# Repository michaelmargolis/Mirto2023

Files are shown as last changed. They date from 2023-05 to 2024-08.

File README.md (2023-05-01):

# Mirto2023
This repository contains software and CAD files for the 2023 version of
the Middlesex University robot platform used for CS and outreach.

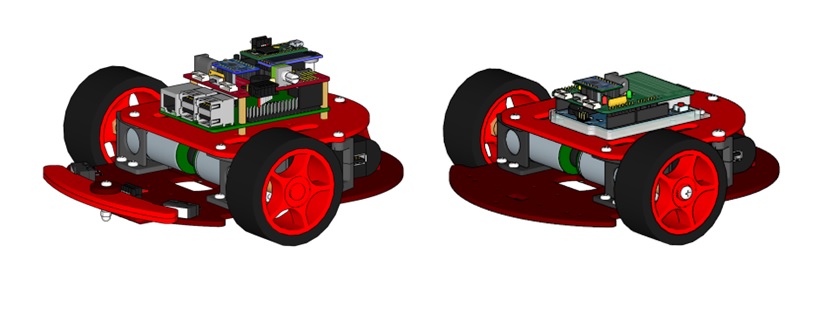
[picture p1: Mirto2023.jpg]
Mirto 2023


Build documentation

This version supports the following variants:
* CS Mirto using Teensy 3.2 board and Raspberry Pi 
  * Teensy drives robot hardware
  * Pi supports robot logic in high level language (python, racket etc)
  * Communication between teensy and Pi using ASIP protocol (see ASIP 1.2 repo)
  * two legacy PCBs are supported:
    * Mirto2016 board that uses Toshiba TB6612FNG H-Bridge
    * Mirto2018 board using TI DRV8833 H-Bridge
  
* CS Mirto using Pico 2040 and Raspbery Pi
  * similar to above but using Pico instead of Teensy
  
* Outreach Mirto using Pico WiFI
  * Uses same Pico PCB as CS pico but without Raspberry pi
  * ASIP protocol over WiFI connects to Scratch or similar
  
* Outreach Mirto using Arduino Wifi R2
  * Uses custom shield for H-Bridge and other robot hardware support
  * ASIP protocol over WiFI connects to Scratch or similar
  
* Standalone Mirto
  * This comprises any of the above without the Raspberry PI
  * Robot logic onboard in C++ or micropython depending on microcontroller

See the ASIP 1.2 repository for code needed for the CS version 

A research paper providing context for use of this robot at Middlesex University can be found here https://eprints.mdx.ac.uk/24368/

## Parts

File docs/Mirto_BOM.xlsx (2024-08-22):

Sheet: Mirto2023
Pico Robot |  | Nbr of Robots | 15
Description | order link | Quantity (per robot) | Total quantity | On hand
PCB Components (Farnell unless indicated)
1K resistor | 9343253 | 2 | 30 |  | all resistors are 1/8th watt
330R resistor | 9343032 | 2
100uF cap | 1870997 | 1 | 15
0.1uF cap | 1141775 | 3 | 45
2.2uF cap | 1827838 | 1 | 15
4.7k resistor network | 9356100 | 2 | 30
PMEG3050EP 5A schottky | 1829197 | 2 | 30
Motor switch | 1201431 | 1 | 15
1N4148 | 9843680 | 1 | 15
BAT46 | 9801456 | 1 | 15
3mm red led | 1581112 | 1 | 15
3mm green led | 1581114 | 1 | 15
8 pin female header | 1593463 | 1 | 15
6 pin female header | 1593462 | 1 | 15
20 pin female header | 1593469 | 2 | 30
2x3 female IDC receptacle | 2215230 | 1 | 15
2x2 female IDC receptacle | 2886085 | 1 | 15
motor connectors | 9491848 | 2 | 30 |  | JST ZH
DC Jack | 224959 | 1 | 15
drv8833 adafruit h-bridge | 1528-1795-ND | 1 | 15 |  | digikey (or https://www.aliexpress.com/item/CJMCU-8833-DRV8833-stepper-motor-drive-control-dual-channel-H-bridge-motor-drive-module-winder/32862868838.html
5mm or 8mm neopixel | ADA1938 | 1 | 15 |  | pihut SKU: ADA1938
1.14 inch 240x135 LCD | WAV-18231 | 1 | 15 |  | Waveshare - pihut etc
20cm USBA to DC 2.1 barrel |  | 1 | 15 |  | https://www.aliexpress.com/item/USB-to-5-5-2-1mm-DC-Power-Barrel-Jack-Plug-5-5-x-2-1/32879860036.html
Male break-away headers |  |  |  |  | We should have in labs
Hardware
M3 12mm | 1420391 | 4 | 60 |  | Packs of 100, adjust order quantity accordingly
M3 8mm | 1419987 | 12 | 180 |  | Packs of 100, adjust order quantity accordingly
M3 5mm button head |  | 4 | 60 |  | Packs of 100, adjust order quantity accordingly
M3 nut | 1419447 | 16 | 240 |  | Packs of 100, adjust order quantity accordingly
M4 8mm | 1419992 | 6 | 90 |  | Packs of 100, adjust order quantity accordingly
1/10 scale wheels | AliExpress | 2 | 30 |  | https://www.aliexpress.com/item/4Pcs-lot-Rubber-63mm-Wheel-Flat-run-Tires-Wide-26mm-On-Road-For-1-10-RC/32759346320.html
Caster |  | 1 | 15 |  | https://www.bearingboys.co.uk/Light-Duty--Saturn-Type/LD16-Chrome-Ball-Transfer-Unit-48126-p
USB power pack |  | 1 | 15 |  | https://www.amazon.co.uk/dp/B019GJLER8
3D and acrylic parts |  |  |  |  | https://livemdxac-my.sharepoint.com/:f:/r/personal/m_margolis_mdx_ac_uk/Documents/Mirto%20Design%20Files/Arduino%20Robot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
motor bracket |  | 2 | 30
wheel hub |  | 2 | 30
acrylic parts
Alternative options for power cable
DC barrel cable | CP-2189-ND |  |  | digikey
USB A plug | 1175-1009-ND |  |  | digikey

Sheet: Arduino Mirto
Arduino Robot |  | Nbr of Robots | 12
Description | order link | Quantity (per robot) | Total quantity | On hand
PCB Components (Farnell unless indicated)
1K resistor | 9339051 | 3 | 36 | * | * Std 1/4 watt, we can use parts in labs
680 ohm | 9339655 | 1 | 12 | * | * Std 1/4 watt, we can use parts in labs
4.7k resistor network | 9356100 | 1 | 12
STPS2L60 2A schottky | 9907637 | 1 | 12
Motor switch | 1201431 | 1 | 12
3mm red led | 1581112 | 1 | 12
3mm green led | 1581114 | 1 | 12
3mm orange led | 1581141 | 1 | 12
8 pin female header | 1593463 | 1 | 12
6 pin female header | 1593462 | 1 | 12
motor connectors | 9491848 | 2 | 24 |  | JST ZH
DC Jack | 224959 | 1 | 12
drv8833 adafruit h-bridge | 1528-1795-ND | 1 | 12 |  | digikey (or https://www.aliexpress.com/item/CJMCU-8833-DRV8833-stepper-motor-drive-control-dual-channel-H-bridge-motor-drive-module-winder/32862868838.html
20cm USBA to DC 2.1 barrel |  | 1 | 12 |  | https://www.aliexpress.com/item/USB-to-5-5-2-1mm-DC-Power-Barrel-Jack-Plug-5-5-x-2-1/32879860036.html
Male break-away headers |  |  |  |  | We should have in labs
Hardware
M3 12mm | 1420391 | 4 | 48 |  | Packs of 100, adjust order quantity accordingly
M3 8mm | 1419987 | 12 | 144 |  | Packs of 100, adjust order quantity accordingly
M3 5mm button head |  | 4 | 48 |  | Packs of 100, adjust order quantity accordingly
M3 nut | 1419447 | 16 | 192 |  | Packs of 100, adjust order quantity accordingly
M4 8mm | 1419992 | 6 | 72 |  | Packs of 100, adjust order quantity accordingly
1/10 scale wheels | AliExpress | 2 | 24 |  | https://www.aliexpress.com/item/4Pcs-lot-Rubber-63mm-Wheel-Flat-run-Tires-Wide-26mm-On-Road-For-1-10-RC/32759346320.html
Caster |  | 1 | 12 |  | https://www.bearingboys.co.uk/Light-Duty--Saturn-Type/LD16-Chrome-Ball-Transfer-Unit-48126-p
USB power pack |  | 1 | 12 |  | https://www.amazon.co.uk/dp/B019GJLER8
3D and acrylic parts |  |  |  |  | https://livemdxac-my.sharepoint.com/:f:/r/personal/m_margolis_mdx_ac_uk/Documents/Mirto%20Design%20Files/Arduino%20Robot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
motor bracket |  | 2 | 24
wheel hub |  | 2 | 24
acrylic parts
Alternative options for power cable
DC barrel cable | CP-2189-ND |  |  | digikey
USB A plug | 1175-1009-ND |  |  | digikey

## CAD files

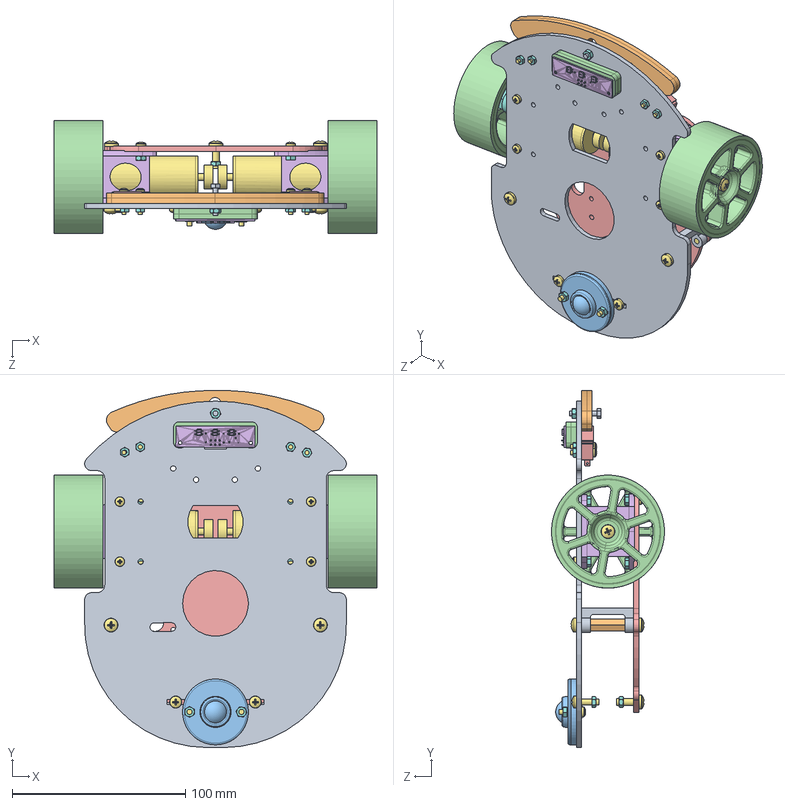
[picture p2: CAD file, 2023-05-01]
CAD/3D/Assembly/mirto2023.SLDASM
186.5 x 206.3 x 65.3 mm
top_plate
ir_spacer x 2
caster_spacer
bumper x 2
bottom_plate
Hotec Motor Mountv2 x 2
hotec_motor x 2
Motor hub x 2
offset_standoff
m4 standoffx30
ball wheel
1_10-drift-tire x 2
microswitch x 2
ir board
pan cross head_am x 23
hex nut style 1_am x 17
hex screw_am

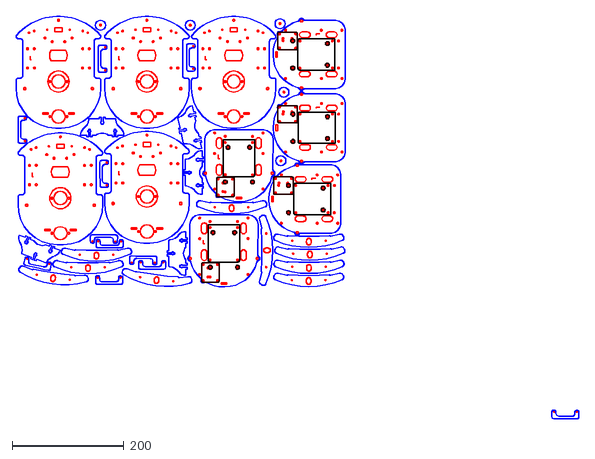
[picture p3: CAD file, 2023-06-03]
CAD/2D/arduino robot half sheet r12.dxf
1007.9 x 720.2

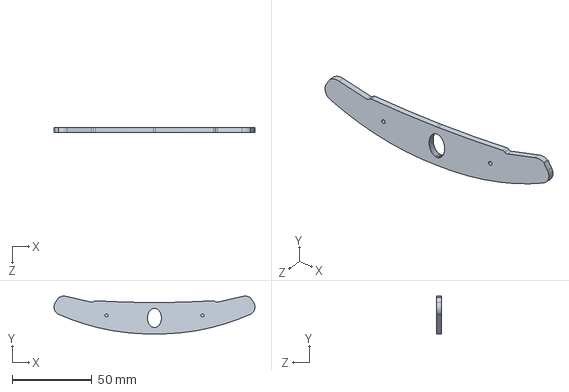
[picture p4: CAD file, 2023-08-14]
CAD/3D/Assembly/bumper.SLDPRT
125.7 x 23.7 x 3.00 mm

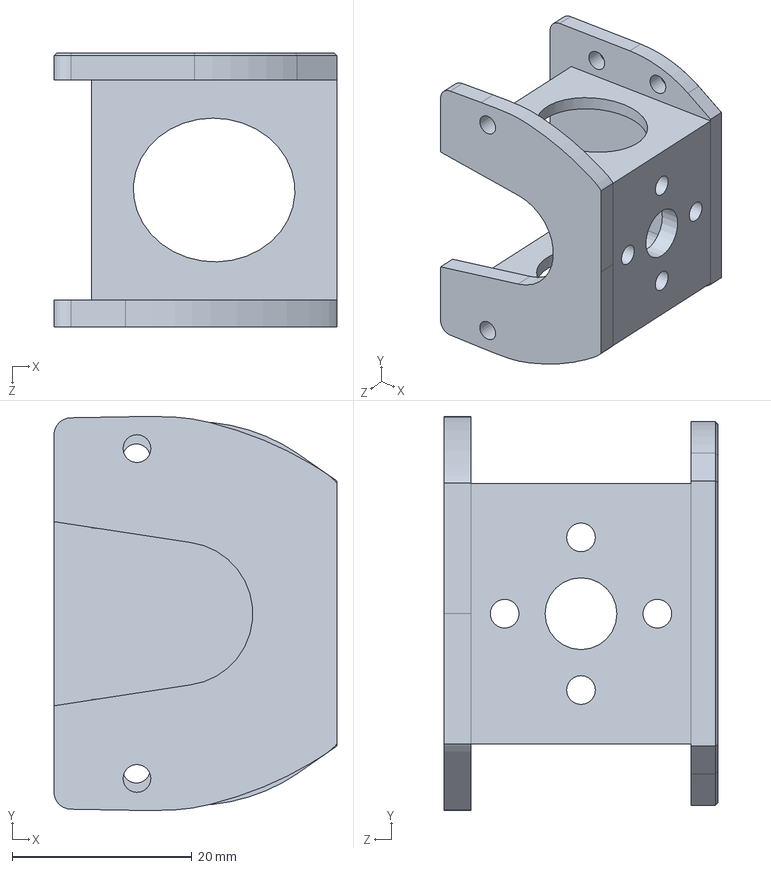
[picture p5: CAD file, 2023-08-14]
CAD/3D/Solidworks/Hotec Motor Mountv2.SLDPRT
31.5 x 43.9 x 30.5 mm

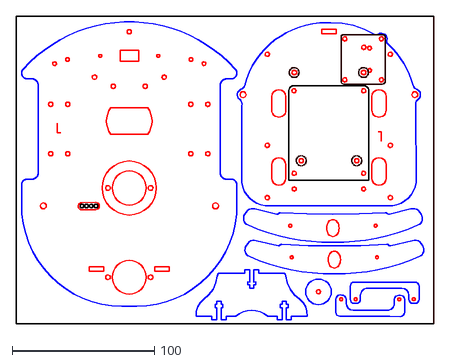
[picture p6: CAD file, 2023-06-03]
CAD/2D/one mirto2023.dxf
293.4 x 216.3

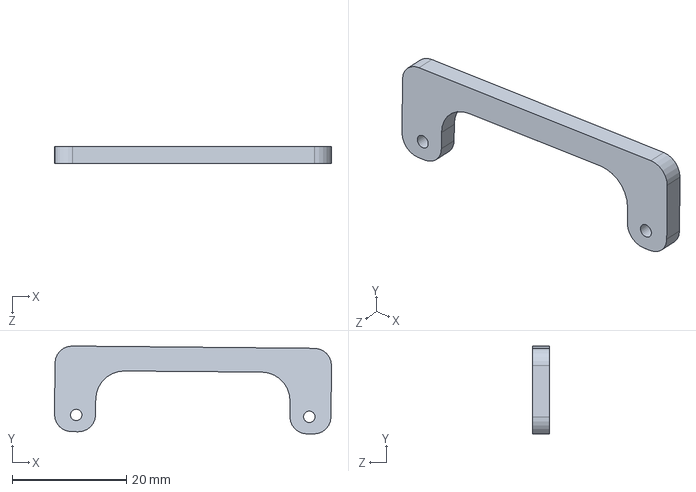
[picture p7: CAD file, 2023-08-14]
CAD/3D/Assembly/ir_spacer.SLDPRT
48.5 x 15.4 x 3.00 mm

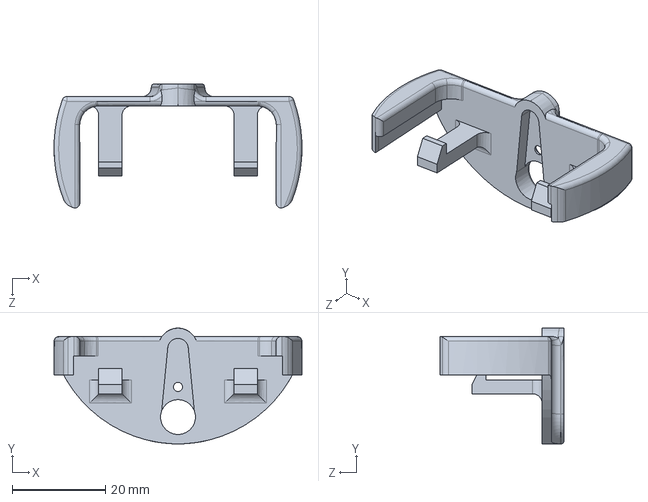
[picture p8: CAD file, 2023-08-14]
CAD/3D/Solidworks/hc_sro4_holder_v2.SLDPRT
53.1 x 24.8 x 26.6 mm

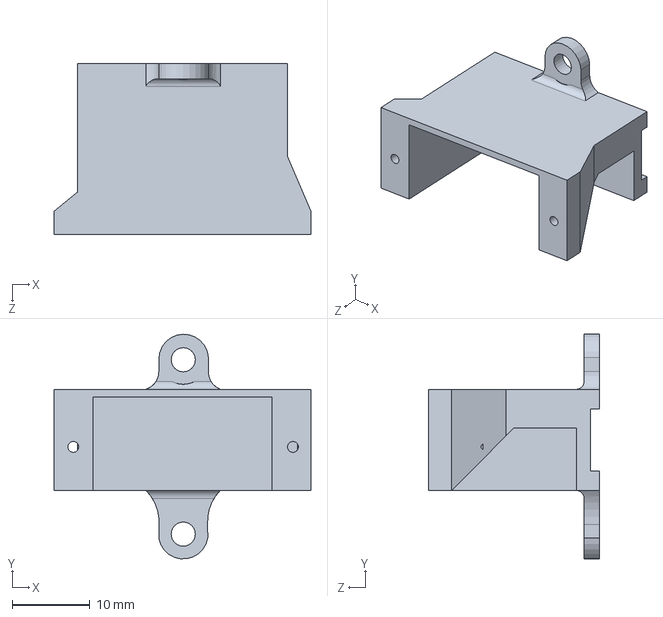
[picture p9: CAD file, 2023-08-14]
CAD/3D/Solidworks/9g servo mount.SLDPRT
33.0 x 28.8 x 22.0 mm

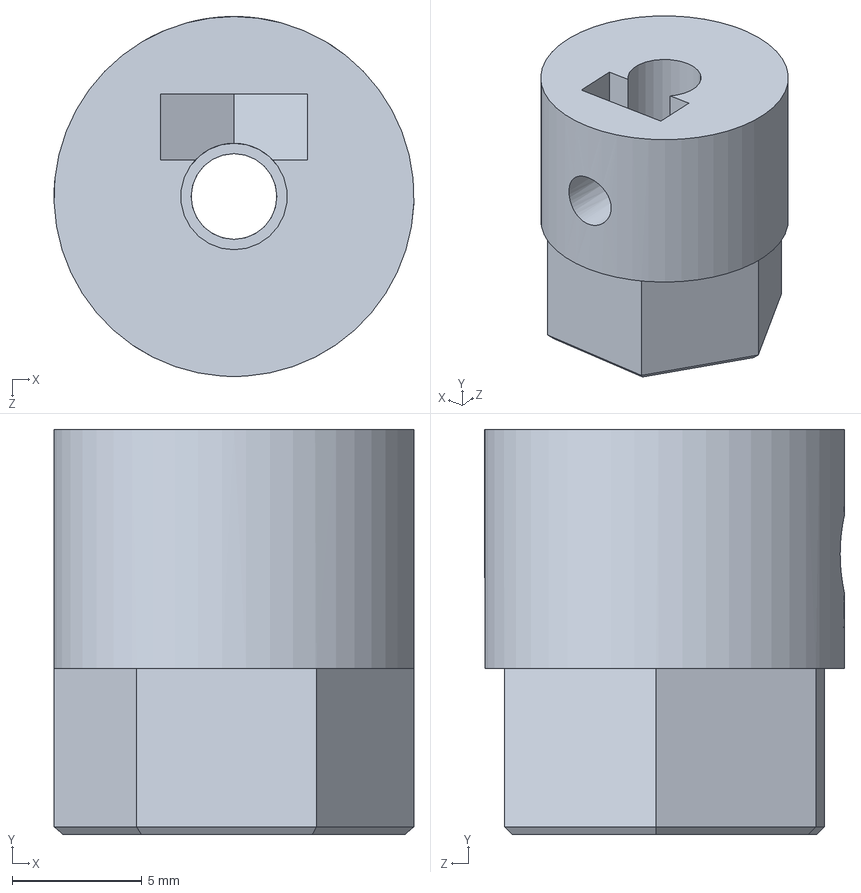
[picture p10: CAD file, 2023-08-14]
CAD/3D/Solidworks/Motor hub.SLDPRT
13.8 x 15.6 x 13.9 mm

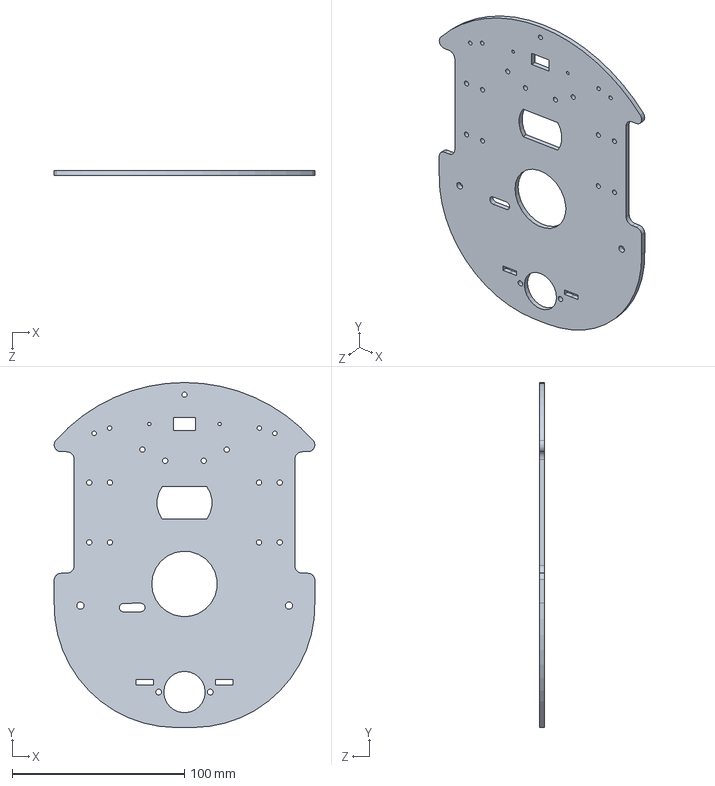
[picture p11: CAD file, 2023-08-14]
CAD/3D/Assembly/bottom_plate.SLDPRT
151.3 x 200.2 x 3.00 mm

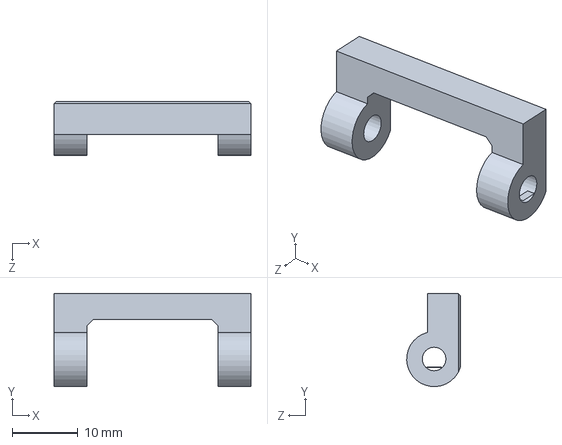
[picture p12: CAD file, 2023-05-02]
CAD/3D/Solidworks/offset_standoff.SLDPRT
30.0 x 14.2 x 8.17 mm

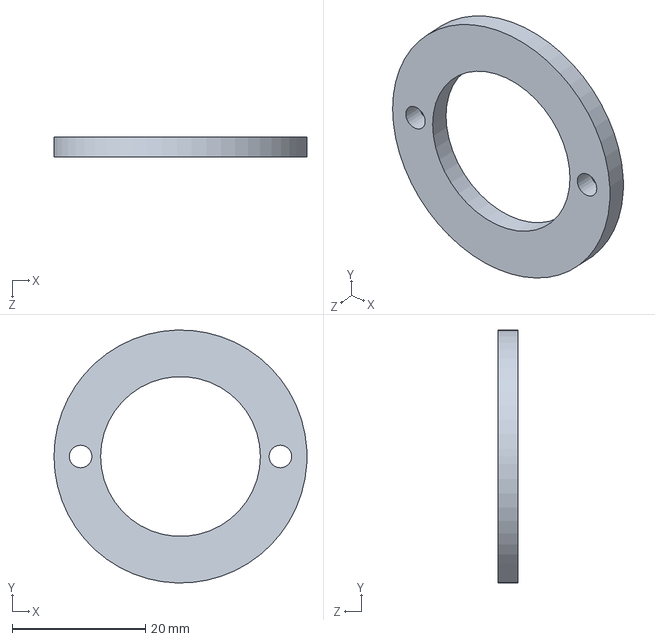
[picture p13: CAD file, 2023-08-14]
CAD/3D/Assembly/caster_spacer.SLDPRT
38.0 x 38.0 x 3.00 mm

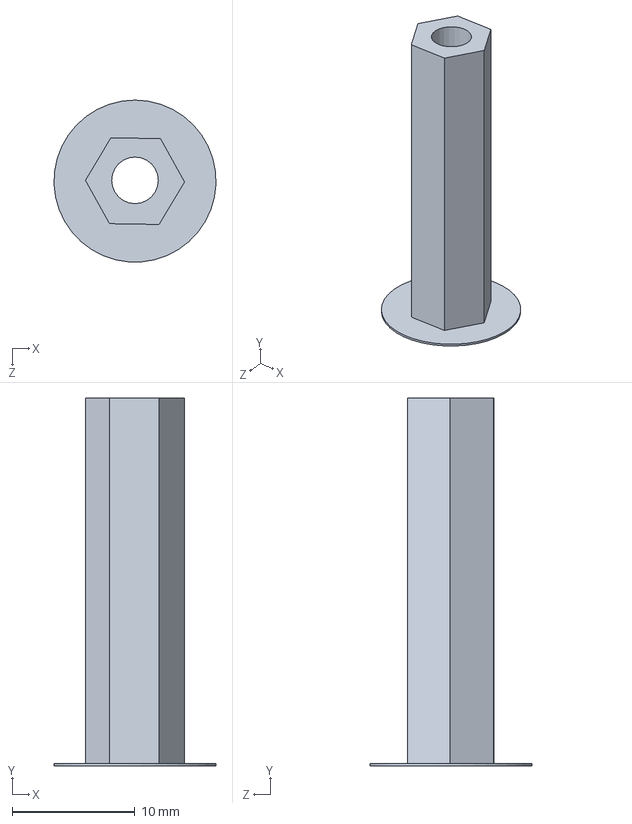
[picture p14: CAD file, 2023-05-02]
CAD/3D/Solidworks/m4 standoffx30.SLDPRT
13.2 x 30.0 x 13.2 mm

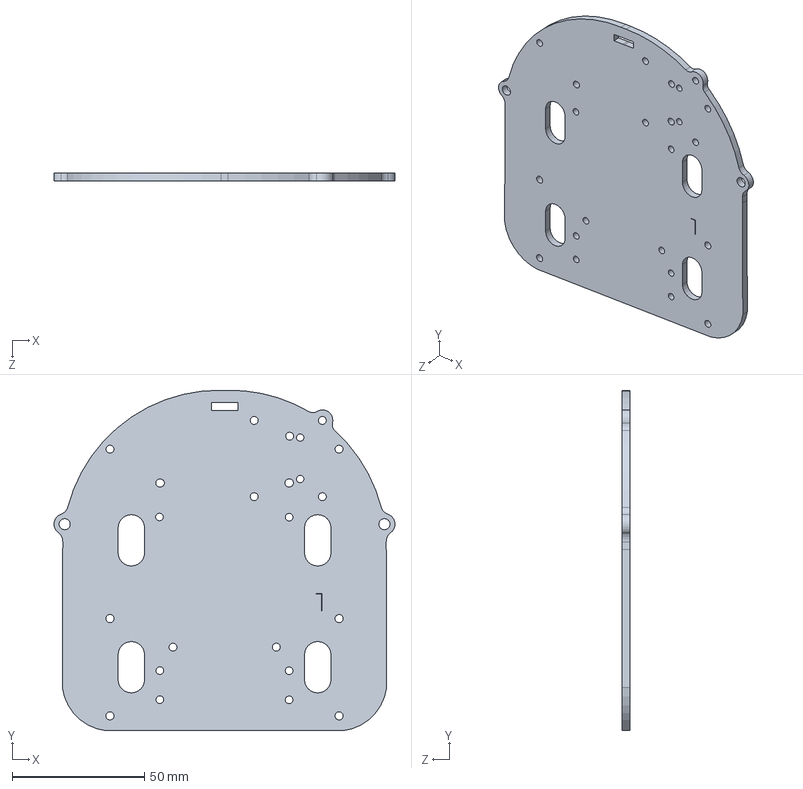
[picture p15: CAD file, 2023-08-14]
CAD/3D/Assembly/top_plate.SLDPRT
128.8 x 128.6 x 3.00 mm

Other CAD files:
CAD/3D/Assembly/rear_upright.SLDPRT
CAD/3D/Assembly/bumper_cap.SLDPRT
CAD/3D/Solidworks/rcwl-1601_holder.SLDPRT
CAD/3D/Assembly/acrylic parts.SLDPRT
CAD/3D/Assembly/top_plate.DXF

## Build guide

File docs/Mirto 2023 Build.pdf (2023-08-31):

1

## Mirto 2023 Build Information

This document describes the Pi Pico variant of the Mirto robot.
The robot can be built with or without bump, distance or IR line sensors.

Document Version 0.6 (draft)
Last updated Aug 30 2023 by Michael Margolis

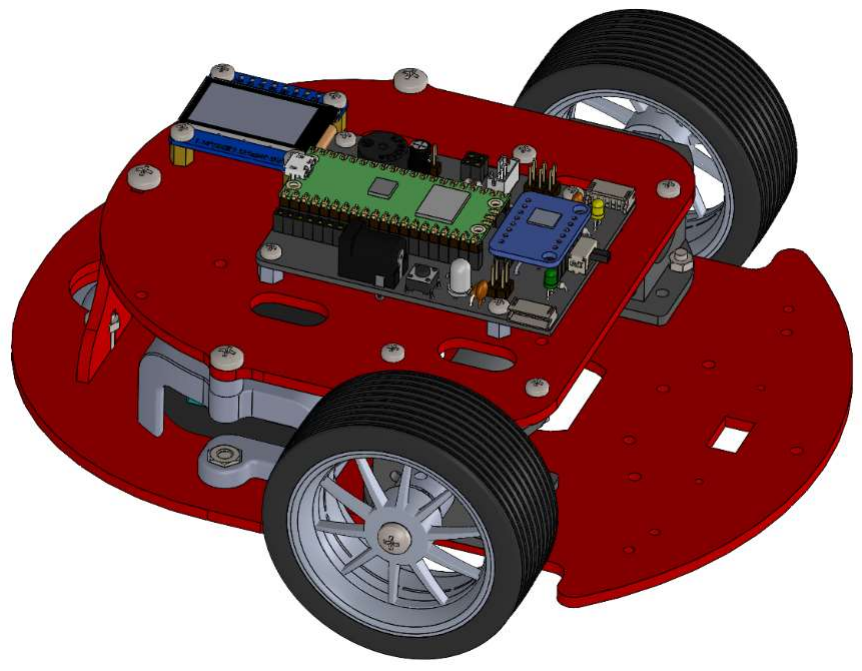
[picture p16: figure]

Figure 1: Basic chassis

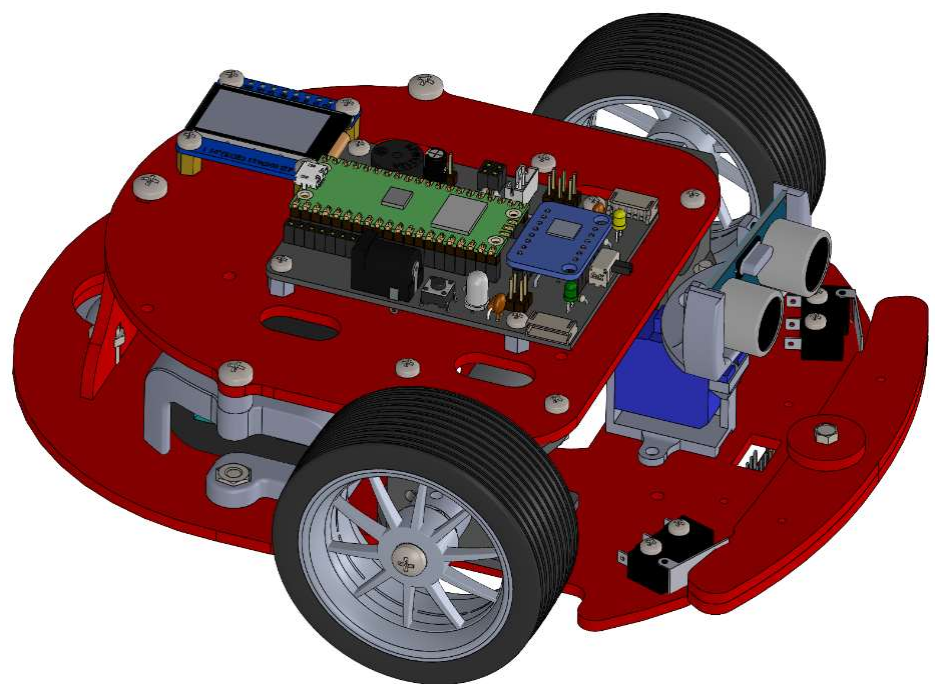
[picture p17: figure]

Figure 2: Chassis with bump , distance, and IR line sensors

2

### Mirto Variants

The Mirto robot can be configured with various sensors to detect the environment and can be controlled using a variety of computer boards. These configurations can be changed at any time by adding or removing components but the initial build is easiest if the desired configuration is built in the sequence shown in this document.

Build sequence tips:
1. The build starts with the bottom plate. Motors are attached and the desired sensors are added. You can skip over sections describing sensor that are not required for your build.
2. The electronics boards are attached to the top plate.

### 3. The electrical connections between the bottom and top plates are easier if done before

bolting the top and bottom together.

### 4. Some of the mounting hardware used for attaching the top and bottom plates differs

depending on the battery being used. See the relevant section covering the battery type used in your build.

Sensor options:
o Bump sensors
o IR line sensors
o Ultrasonic distance sensor
o Mounted on servo (pico version only) o Fixed
o Lidar (not covered in this document)

Microcontroller options:
o Arduino WiFI R2 with Mirto shield
o Mirto PCB with Pico WiFi
o Mirto PCB with Pico (not WiFi) and Raspberry Pi) o Mirto Teensy PCB and Raspberry Pi

Power options:
o Generic USB power bank
o USB bank with custom mount (Currently Anker PowerCore 5k and Anker PoweCore 10k)

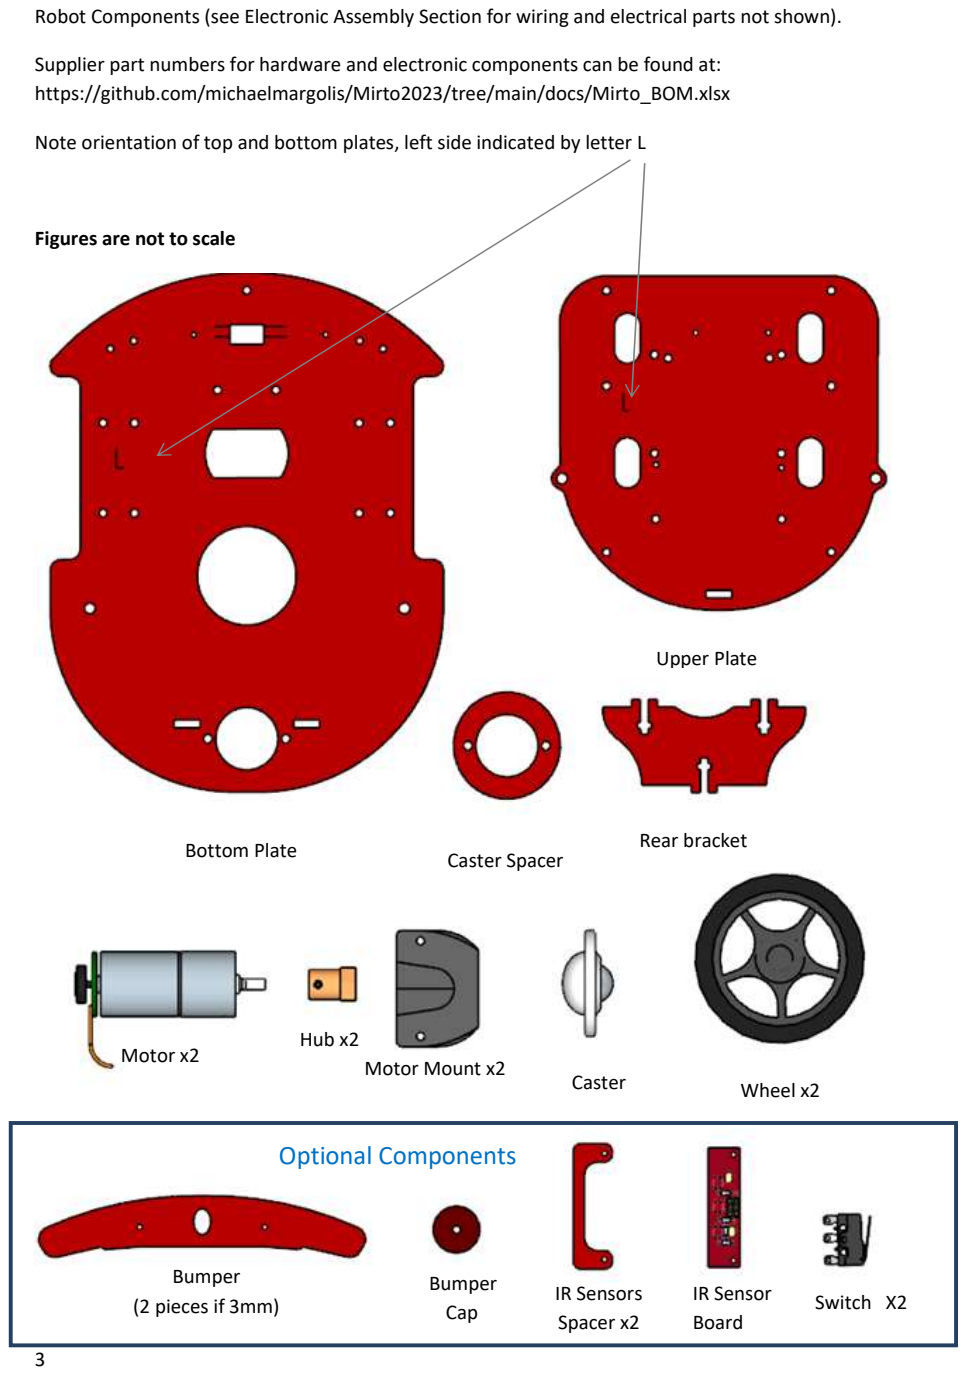
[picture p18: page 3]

3

Robot Components (see Electronic Assembly Section for wiring and electrical parts not shown).

Supplier part numbers for hardware and electronic components can be found at: https://github.com/michaelmargolis/Mirto2023/tree/main/docs/Mirto_BOM.xlsx

Note orientation of top and bottom plates, left side indicated by letter L

Figures are not to scale

Bottom Plate

Upper Plate

Bumper
(2 pieces if 3mm)

Caster

Caster Spacer

IR Sensors
Spacer x2

Bumper
Cap

Rear bracket

Motor Mount x2

Offset Spacer

Motor x2

IR Sensor
Board

Wheel x2

Hub x2

Switch X2

### Optional Components

4

Hardware for core robot:

Quantity | Description
21 M3 X 12 pan or button head machine screw

21 M3 nut
4 M4 X 8 pan head machine screw

Hardware for motor mounts: (Already attached if motor mounts are pre build)

Quantity | Description
4 M3 x 5 socket button head machine screw

2 M3 Grub screw

2 M3 nut

Additional hardware for robot with bump sensors
Quantity | Description
1 M3 X 20 socket button screw

1 M3 locknut

1 Nylon dome nut

4 M2.5 x 12 pan head machine screw 4 M2.5 nut

Additional Hardware for robots with IR Sensors
Quantity | Description
2 M2 X 12 pan head machine screw
2 M2 nut

Additional Hardware for robots with Waveshare 1.14 inch IPS-TFT-LCD Display (SKU 18231)
Quantity | Description
4 M3x5 machine screw (or button head)

5

Hardware for mounting controller boards:

Arduino Robot controller mounting hardware (For Arduino Uno Wifi and PCB)
Quantity | Description
4 M3 x 8 pan head machine screw

4 M3 nut

CS Robot mounting hardware (for Raspberry Pi and Mirto PCB)
Quantity | Description
8 M2.5 x 12 pan head machine screw

4 M2.5 x 4 threaded standoff for Pi

4 M2.5 x 16 threaded standoff for Mirto PCB

Useful tools:

Screwdrivers /hex keys for machine screws and grub screws
M4 tap for 3D printed hubs and standoffs ( if printed tolerance does not allow self threading)

Build notes:

- Read through all steps before beginning assembly
- Double check hardware before each assembly step and make sure that the length of the screw matches the instructions.
- Look at the prototype if you are not sure how things go together
- Don’t overtighten the screws
- Machine screws are pan head where not specified.
- If using thread lock, apply only after initial assembly

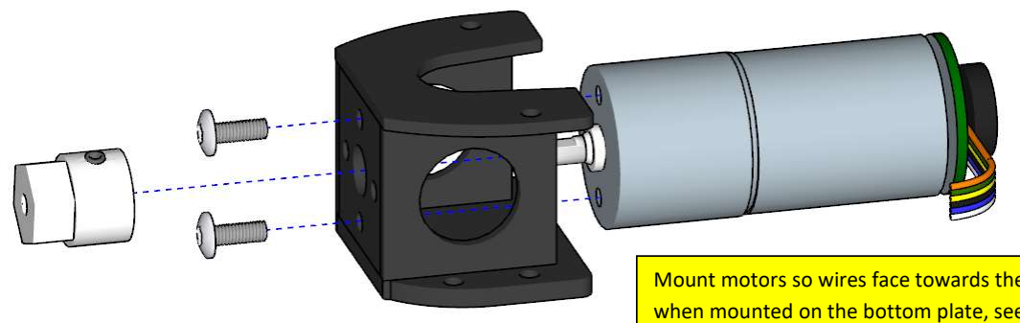
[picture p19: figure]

6

Motor Assembly

You can skip the steps on this page if the motor assemblies are pre-built.

If not already fitted, insert M3 nut into slot on hub and hold in place with grub screw

Attach motors to mount using M3x5 button head screws. Don’t overtighten these screws.

Note left and right motor positions are mirror images, see figure 6.
Caution – you must use the M3x5 hardware specified, longer screws will damage the gearbox!

Hardware: 2 off M3 x 5 socket button screws for each motor

### 2 off M3 grub screws and M3 nuts for hubs

Figure 5: Motor Mount
Attach hub. There should be a slight gap to avoid touching motor screws

Mount motors so wires face towards the rear when mounted on the bottom plate, see Fig 4.

Figure 4: Hub Detail

Figure 3: Completed motor assembly

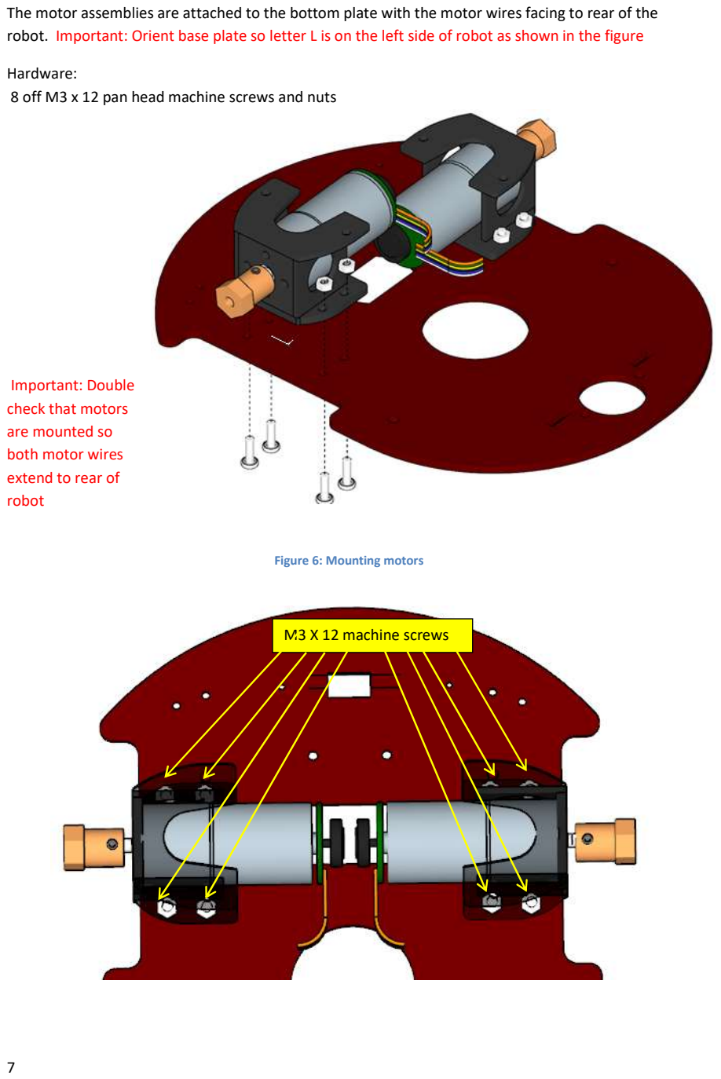
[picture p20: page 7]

7

The motor assemblies are attached to the bottom plate with the motor wires facing to rear of the robot. Important: Orient base plate so letter L is on the left side of robot as shown in the figure

Hardware:

### 8 off M3 x 12 pan head machine screws and nuts

Important: Double
check that motors
are mounted so
both motor wires
extend to rear of
robot

M3 X 12 machine screws

Figure 6: Mounting motors

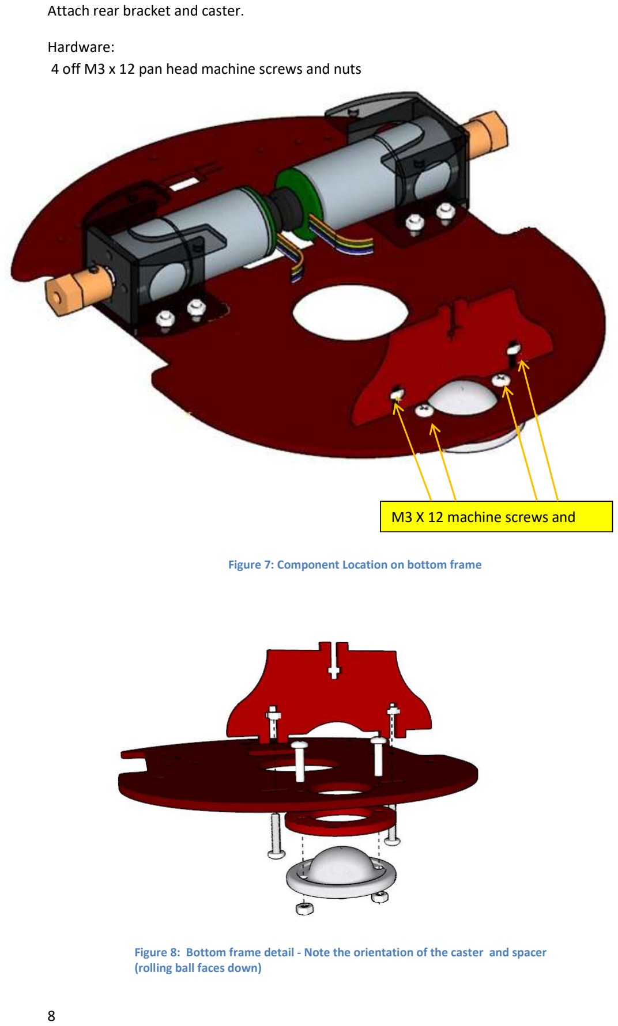
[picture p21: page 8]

8

Attach rear bracket and caster.

Hardware:

### 4 off M3 x 12 pan head machine screws and nuts

Figure 7: Component Location on bottom frame

Figure 8: Bottom frame detail - Note the orientation of the caster and spacer (rolling ball faces down)

M3 X 12 machine screws and

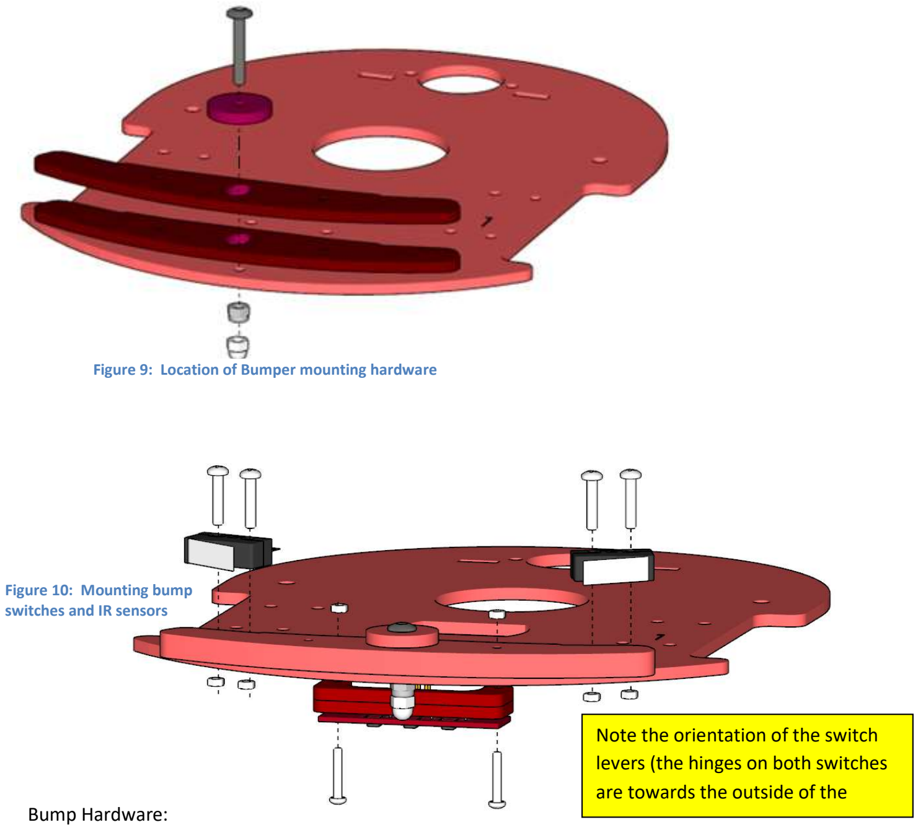
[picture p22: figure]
Bump Hardware:; Figure 10: Mounting bump switches and IR sensors; Note the orientation of the switch levers (the hinges on both switches are towards the outside of the

9

Only do the steps on this page if building the robot with bump switches or IR Sensors.

Attach two bumpers to the lower plate using a 20mm M3 hex machine screw and nyloc nut. The nyloc nut is metal with a nylon insert that resists turning; you will need to hold this nut with pliers when tightening the screw with a hex key until there is just enough play to allow free movement of the bumpers without lifting off the bottom plate. The plastic dome nut is then screwed onto the bottom to act as a skid to prevent the robot tipping forward and damaging the IR sensors.

### 1 off M3 x 20 socket button screw 1 off M3 lock nut 1 off M3 plastic dome nut 4 off M2.5 x 12 pan head screws 4 off M2.5 nuts

Figure 9: Location of Bumper mounting hardware

IR sensor Hardware:

### 4 off M2x12 pan head screws 4 off M2 nuts

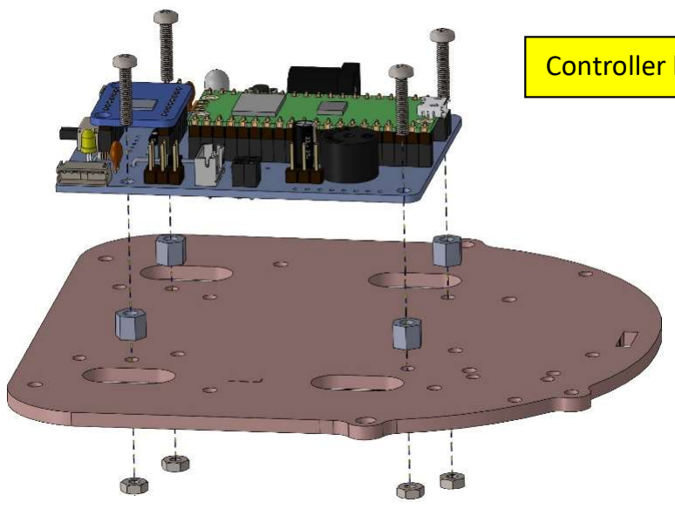
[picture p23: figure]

10

### Top plate electronics- Mirto 2023 Pico W board

Yellow arrows show
mounting hole location.

Controller board mounted using M2.5 X 12 bolts and nuts

Attach display using M3 X5 bolts

Note display orientation, connector faces inwards.

Figure 11: controller attaches to top plate using 5mm high M2.5 spacers

Figure 12: LCD display attaches using M3x5 machine screws

Figure 13: LCD display detail

11

Battery options:

Anker 5k

Attach the right side to the base using M5x8 Machine screw from the underside. The top
Is attached using an M4x16 machine screw.
The other side is attached using an M4x40 machine Screw and nut.

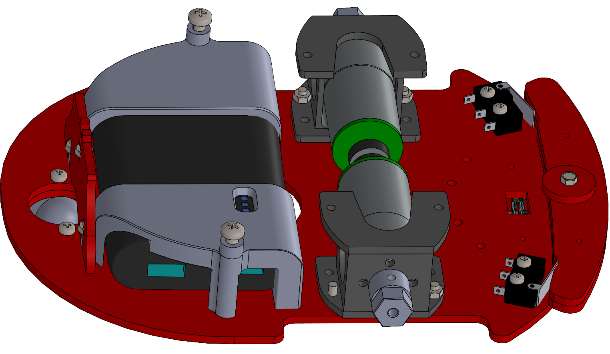
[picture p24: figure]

Anker 10k

Attach using M4x40 machine screws and nuts.

Generic USB power bank

Locate the battery on the bottom plate ensuring the charging and output connectors are accessible. Use an offset standoff on the side near the battery connectors to allow clearance for the power and charging cables. The other side uses a 30mm long M4 standoff.

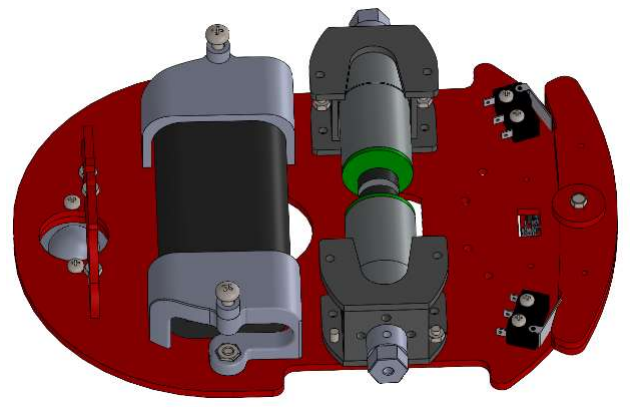
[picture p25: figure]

Figure 14: Anker 5k battery clips

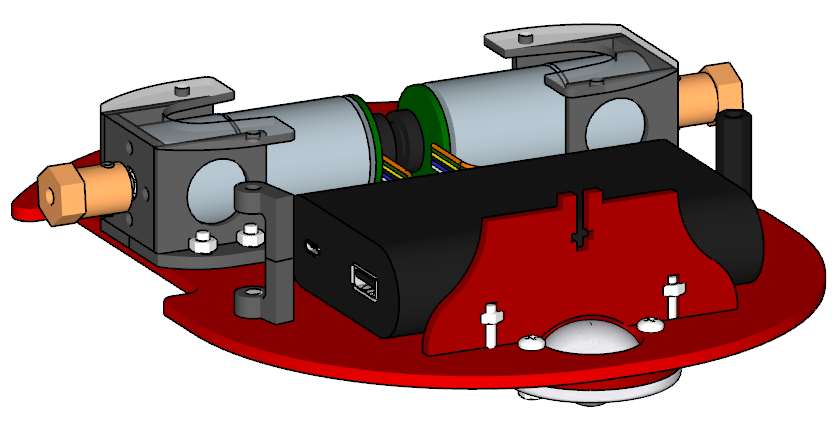
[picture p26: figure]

Figure 16: Generic battery with standoffs

Figure 15: Anker 10 battery clips

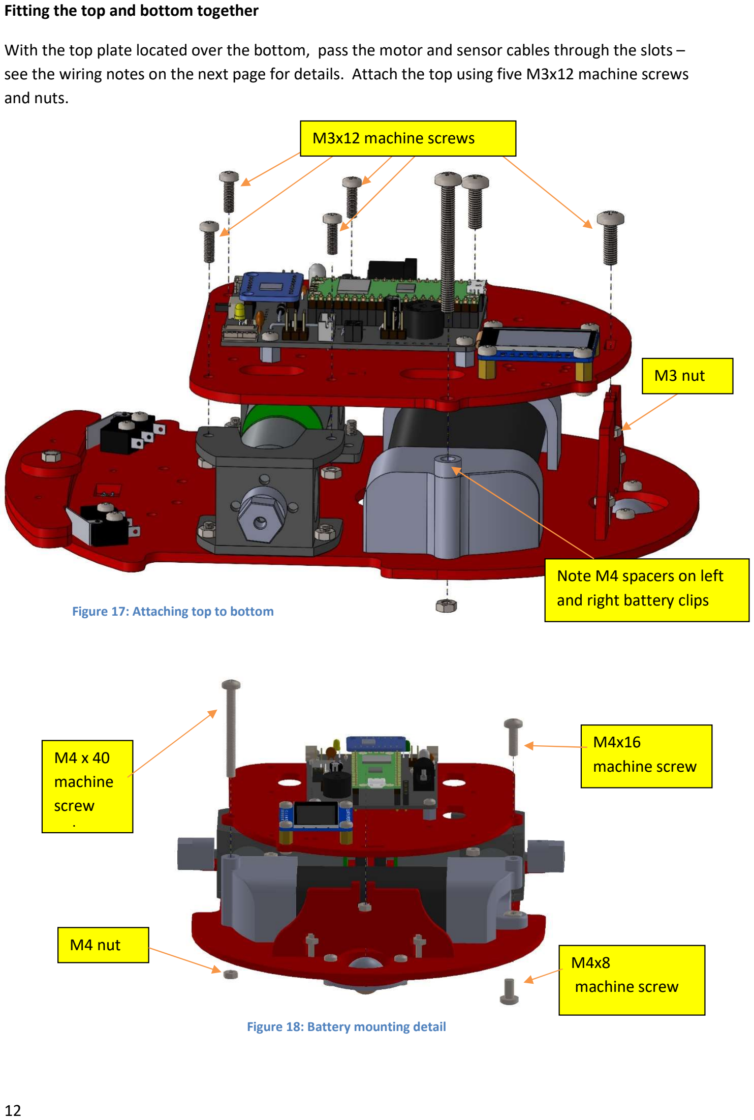
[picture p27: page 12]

12

Fitting the top and bottom together

With the top plate located over the bottom, pass the motor and sensor cables through the slots – see the wiring notes on the next page for details. Attach the top using five M3x12 machine screws and nuts.

M3 nut

Note M4 spacers on left
and right battery clips

M3x12 machine screws

M4 x 40
machine
screw
nut

M4 nut

M4x16
machine screw

M4x8
machine screw

Figure 18: Battery mounting detail

Figure 17: Attaching top to bottom

13

Wiring Notes

Wiring is easiest if completed before the top is mounted to the base.

With the PCB and LCD mounted to the top plate, connect the these together as follows:

- Connect the cable plug onto the 8 pin LCD connector on the PCB.
- Thread the other end of the cable down through the top plate hole nearest the connector and up on the hole nearest the LCD.
- Run the wire under the corner of the PCB and plug the cable into the LCD.

With the top plate loosely positioned over the base:
- Thread the motor wires through holes near each motor
- Thread the four pin bump switch connector through the right hand side motor hole
- Thread the six pin IR connector through the left side motor hole
- If using a servo, thread the servo cable through the hole nearest the LCD

Attach the top and bottom plates as shown in figure 17

Plug in the connectors as shown in the Mirto wiring Figure 19

Plug the battery connector to the round DC connector.

If using the distance sensor, connect the four pin cable as follows:

- The white plug connects to the PCB socket marked Stemma I2C1
- The black end connected to the distance sensor, note the black wire must connected to the side marked GND.

14

Mirto 2023 wiring

Wire colors may vary on the LCD cable. Ensure that the order of the colors on the LCD connecter is the same as the PCB connector.

Servo ground
wire this side

LCD cable
through
this hole

IR Cable

Motor
connector

Distance
sensor
Battery
connector

Motor
connector

LCD
connector

Bump
cable

Same
Color
wire

Figure 19: Electrical connections

Micro USB

Test
pushbutton

15

Attach Wheels

Push the wheels onto the hubs and attach with M4X8 machine screws

Hardware:

### 2 M4 x 8 machine screws

Testing the robot:

If the Mirto Arduino sketch has not been loaded, connect the micro USB connector (see figure 19) to a computer with the ASIP Arduino environment and load this sketch: mirtoWifiWebsocket at GitHub michaelmargolis/ASIP-V1.2

With the sketch loaded, power the robot while holding down the test pushbutton (see figure 19). When the LCD displays “Test Mode”, release the button. If all is well, you should hear some tones while the LCD display changes colors. The display will then show readings from the distance sensor and the IR line sensors if these are fitted.

After completing testing, press the pushbutton to restart the robot.

Figure 20: Attach wheels

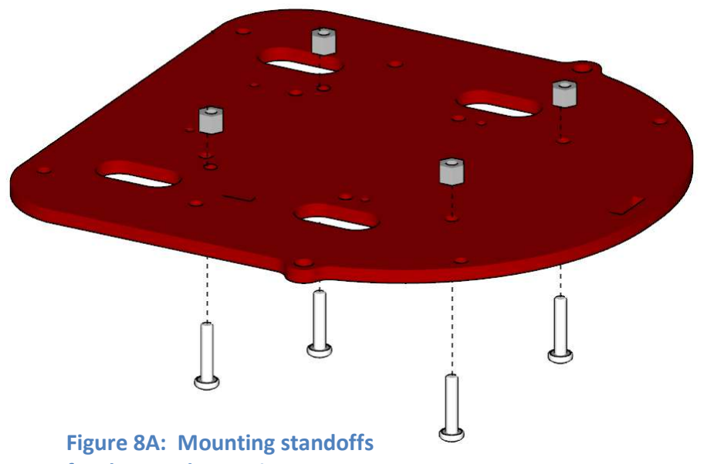
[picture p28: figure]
Figure 8A: Mounting standoffs

16

### Appendix A – Alternative top plate electronics

CS Mirto using Teensy 3.2 or Pico board and Raspberry Pi

Attach four M2.5X4 spacers using M2.5X12 machine screws. Note the location of the holes as shown in figure

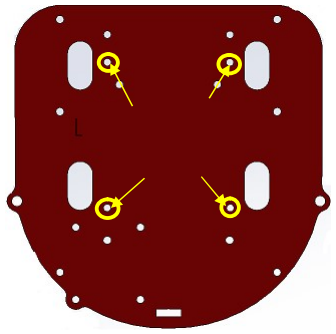
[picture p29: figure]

The Raspberry pi is inserted onto the screws and held in place using four M2.5X16 threaded standoffs. The Mirto2020 PCB is plugged into the Pi and secured using four M2.5X12 machine screws.

Hardware:

### 4 M2.5 x 4 standoffs 4 M2.5 x 16 standoffs 8 M2.5 x 12 machine screws

for the Raspberry Pi

Figure 8B: Location of Raspberry Pi mounting holes

Figure 8C: Raspberry Pi
positioned on standoffs

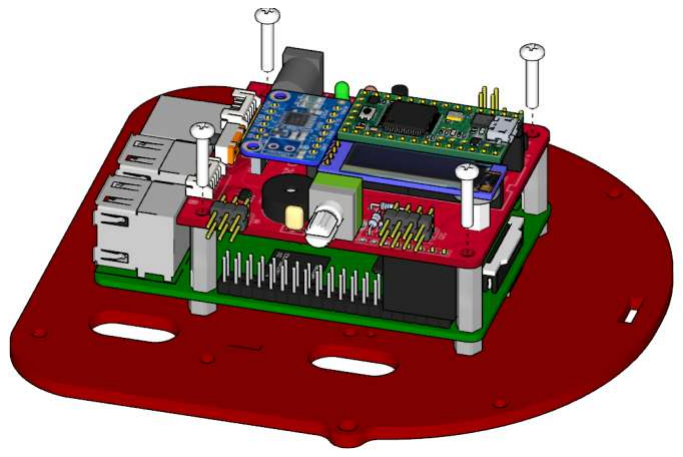
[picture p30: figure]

Figure 8D: Mirto circuit board on top of Pi

17

Boards that do not have build-in LCD display are attached to the top plate using the hole positions

shown below:

Teensy .96 OLED LCD mounting position. | Teensy 1.3 OLED LCD mounting position.

Assembling the Arduino version:

Attach the Arduino mount using four M3x8 machine screws and nuts. The mount is supplied with Arduino Uno WiFi rev 2 or can be ordered from Arduino supplier as part number X000019.
The Arduino board and Mirto PCB can be press fitted to the mount after assembling the robot.

Hardware:

### 4 M3 x 8 machine screws 4 M3 nuts

The Teensy PCBs has an
I2C Display.

Ensure the wires are
connected as per the pin
labels on the display and
the silkscreen markings
on the boards I2C
connector.

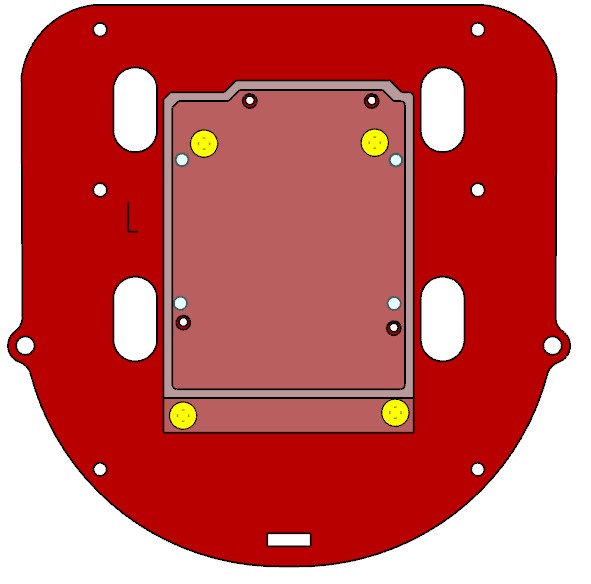
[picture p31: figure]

Figure 9A: Location of mounting holes for Arduino mount

18

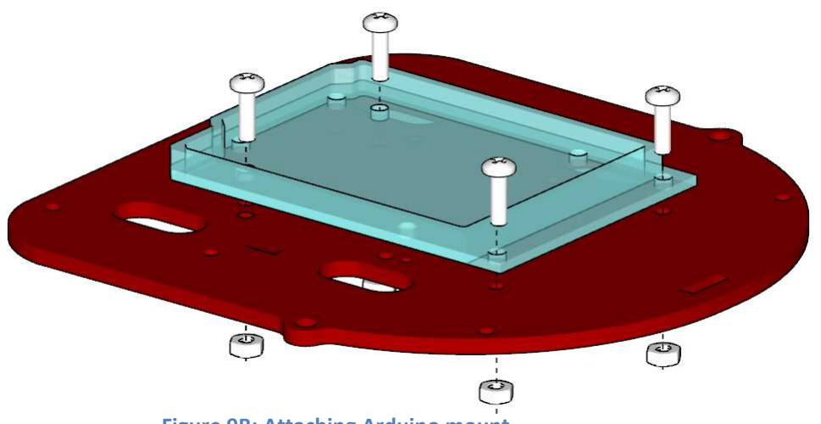
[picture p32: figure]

Figure 9B: Attaching Arduino mount

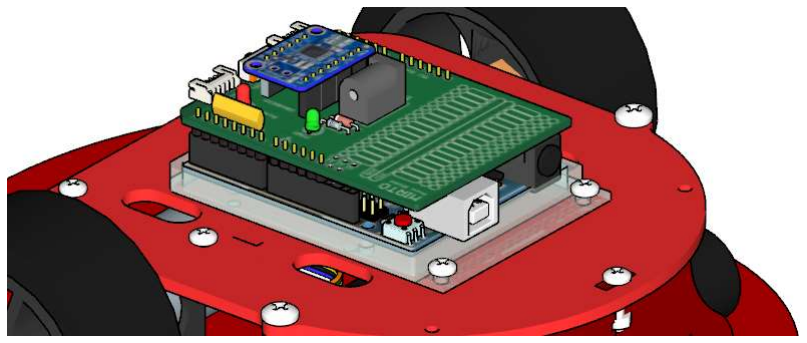
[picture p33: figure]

Figure 9C: Arduino and motor shield located on mount

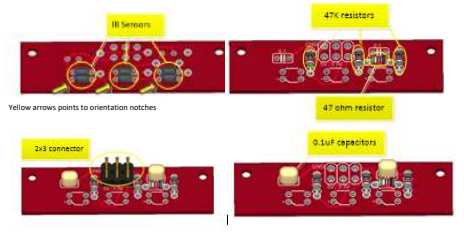
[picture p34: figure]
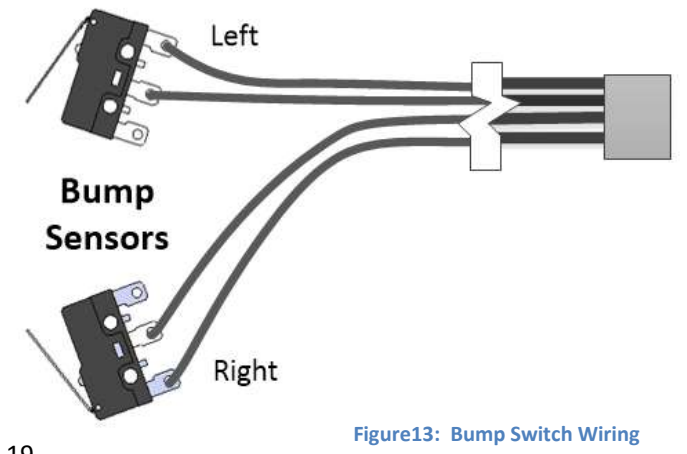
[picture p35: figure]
Figure13: Bump Switch Wiring

19

### Appendix B - Electronic Assembly and Wiring Information

The IR Sensor Connector Board is made by inserting three IR sensors from the underside of the board. Three 47K resistors and one 47 ohm resistor are placed on the upper side of the board. Solder two 0.1 uF ceramic capacitors and the 2x3 connector as shown below.

Yellow arrows points to orientation notches

The IR sensors are connected to the main circuit board using approximately 14cm of 6 conductor IDC cable.

The bump switch assembly is made by soldering approximately 16 cm of four conductor ribbon cable to the switches as shown. The other end is crimped into a 2x2 IDC ribbon connector.

Figure 12: IR Sensor Connector Board

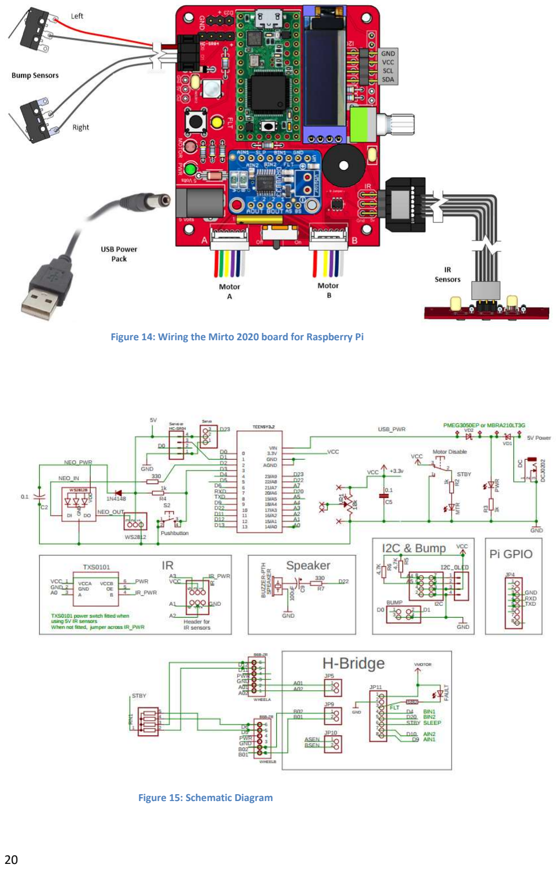
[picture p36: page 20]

20

Figure 14: Wiring the Mirto 2020 board for Raspberry Pi

Figure 15: Schematic Diagram

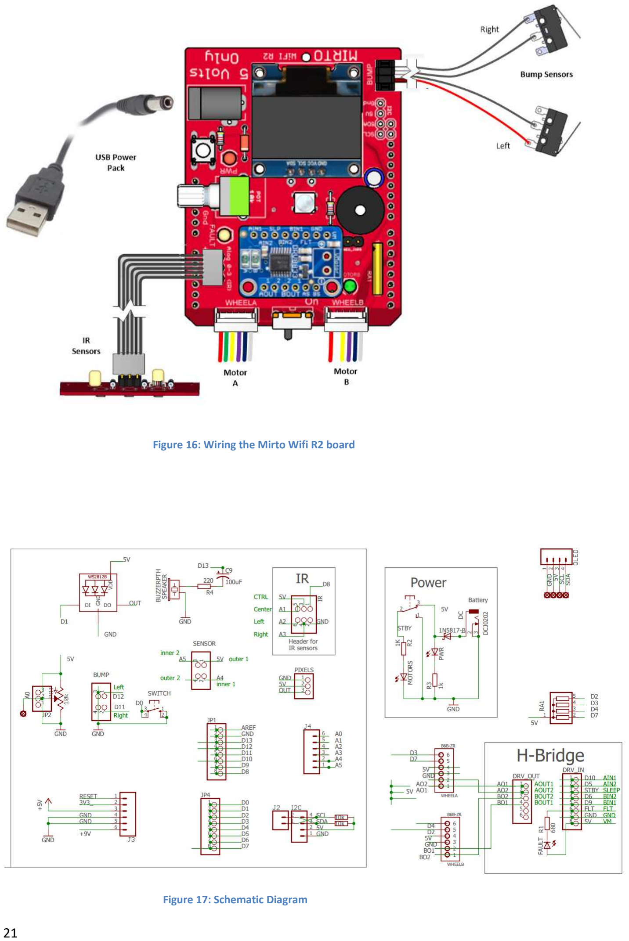
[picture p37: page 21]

21

Figure 16: Wiring the Mirto Wifi R2 board

Figure 17: Schematic Diagram

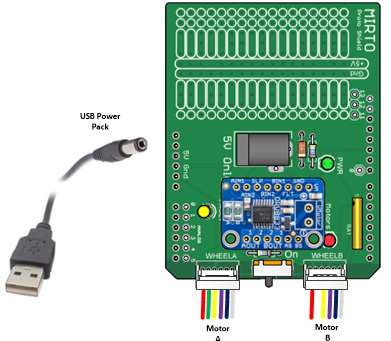
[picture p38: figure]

22

23

RCWL -1601 distance sensor wiring

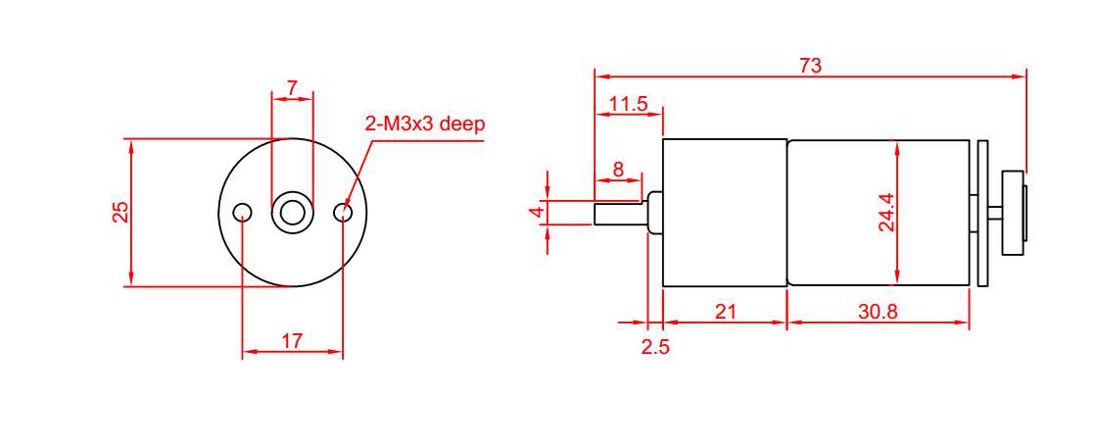
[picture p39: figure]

24

Appendix C - Motor Details

The specifications for the motors measured at 6 volts are as follows:

NO LOAD:
Current: < 0.15 Amps Max
Speed: 197±10%rpm

ON LOAD :
Torque: 0.7kg.cm
Current: < 0.54A Max
Speed: 158±10%rpm

STALL:
Current: < 2.87 Amps
Torque 4kg.cm

Gearbox Ratio 1:34
Maximum Motor Drive Voltage: 8.4 Volts

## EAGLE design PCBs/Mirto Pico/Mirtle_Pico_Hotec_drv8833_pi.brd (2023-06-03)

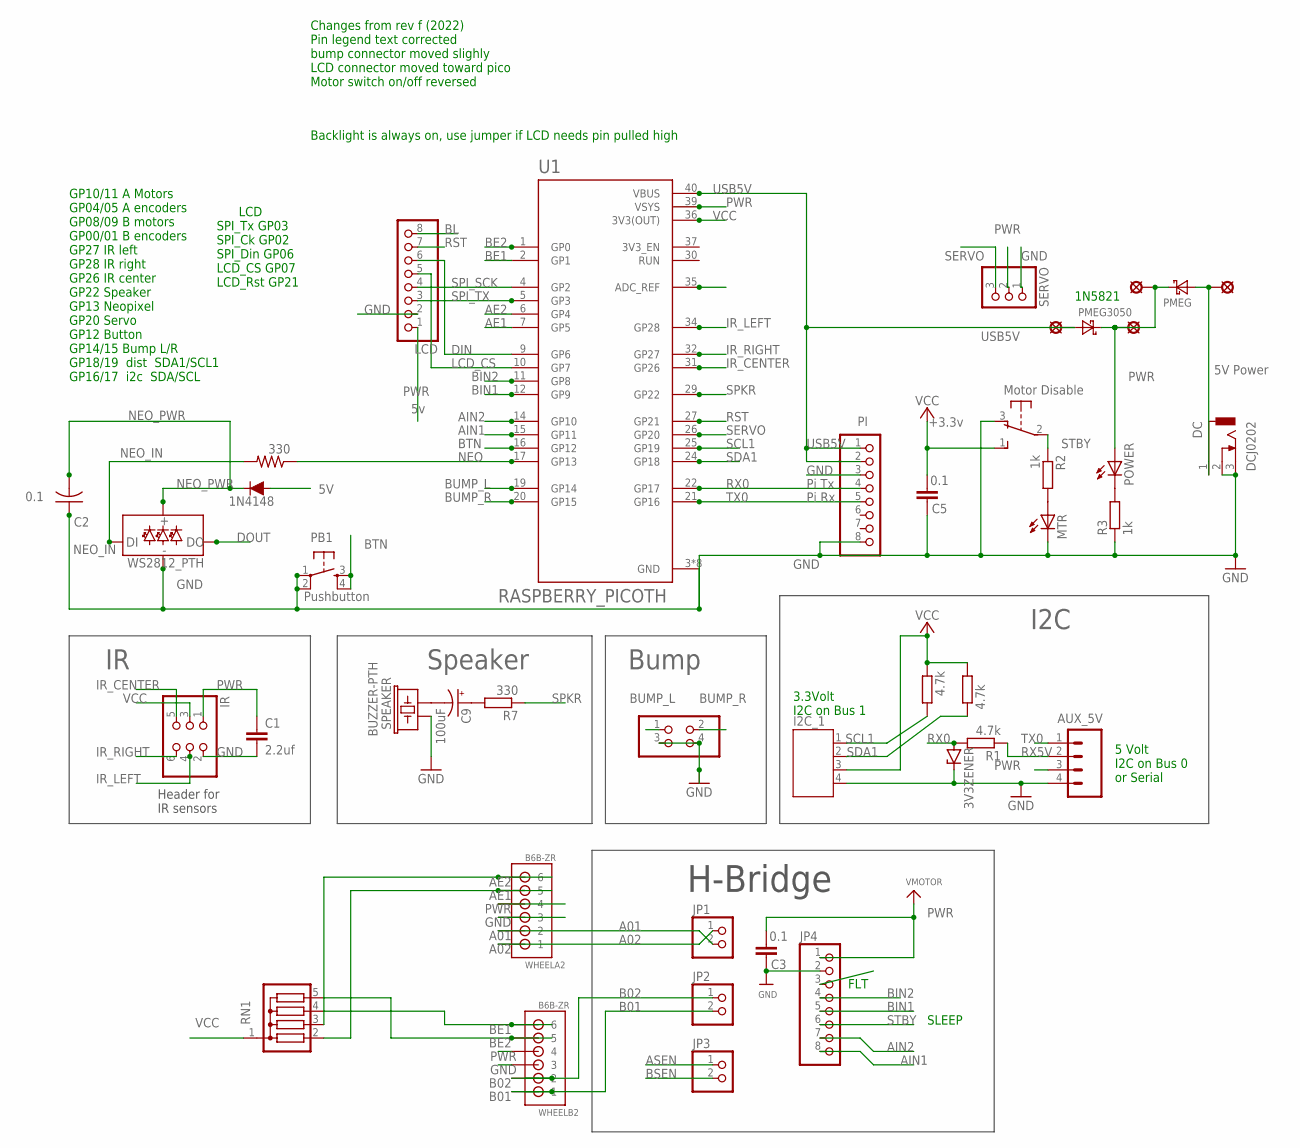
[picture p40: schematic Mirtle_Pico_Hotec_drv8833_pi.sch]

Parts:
3V3ZENER: ZENER-DIODEZD-5; ZDIO-5
AUX_5V: CONN_04; 1X04
BUMP: PINHD-2X2; 2X02
C1: 2.2uf; C5B2.5
C2: 0.1; C025-024X044
C3, C5: 0.1; CAP-PTH-SMALLEZ
C9: 100uF; E2,5-5
D1: WS2812_PTH; WS2812B-PTH-KIT
DC: DCJ0202
I2C_1: JST-PH4
IN4148: 200mA/100V/1V; DIODE-1N4148
IR: PINHD-2X3; 2X03
JP1, JP2, JP3: HEADER-1X2ROUND; 1X02_ROUND
JP4: HEADER-1X870MIL; 1X08_ROUND_70
LCD: PINHD-1X8BIG; 1X08-BIG
LSP1, LSP2, LSP3, LSP4: SE14
MTR: LED3MM
PB1: TAC_SWITCHPTH; TACTILE-PTH
PI: PINHD-1X8BIG; 1X08-BIG
PMEG, PMEG3050: DIODE-SCHOTTKY-SMA; SMA
POWER: LED3MM
R1, R4, R5: 4.7k; 0204/5
R2, R3: 1k; 0204/5
R7, R12: 330; 0204/5
RN1: G04R; SIL5
SERVO: PINHD-1X3; 1X03
SPEAKER: BUZZER-PTH; BUZZER-12MM
SW1: OS102011MA1Q
U1: RASPBERRY_PICOTH; PICO-PKG-TH_MM
WHEELA2: B6B-ZR
WHEELB2: B6B-ZR

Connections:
5VIN: DC.1, LSP3.MP, PMEG.A
A01: JP1.2, WHEELA2.2
A02: JP1.1, WHEELA2.1
AE1: RN1.2, U1.7 (GP5), WHEELA2.5
AE2: RN1.3, U1.6 (GP4), WHEELA2.6
AIN1: JP4.8, U1.15 (GP11)
AIN2: JP4.7, U1.14 (GP10)
ASEN: JP3.1
B01: JP2.2, WHEELB2.1
B02: JP2.1, WHEELB2.2
BE1: RN1.4, U1.2 (GP1), WHEELB2.6
BE2: RN1.5, U1.1 (GP0), WHEELB2.5
BIN1: JP4.5, U1.12 (GP9)
BIN2: JP4.4, U1.11 (GP8)
BL: LCD.8
BSEN: JP3.2
BTN: PB1.3, PB1.4, U1.16 (GP12)
BUMP_L: BUMP.1, U1.19 (GP14)
BUMP_R: BUMP.2, U1.20 (GP15)
DIN: LCD.6, U1.9 (GP6)
DOUT: D1.DO
GND: 3V3ZENER.C, AUX_5V.4, BUMP.3, BUMP.4, C1.2, C2.1, C3.1, C5.1, D1.GND, DC.2, DC.3, I2C_1.4, IR.2, JP4.2, LCD.2, MTR.K (C), PB1.1, PB1.2, PI.3, PI.8, R3.1, SERVO.1, SPEAKER.+ (1), SW1.3 (O), U1.3 (GND), U1.8 (GND), U1.13 (GND), U1.18 (GND), U1.23 (GND), U1.28 (GND), U1.33 (GND), U1.38 (GND), WHEELA2.3, WHEELB2.3
IR_CENTER: IR.5, U1.31 (GP26)
IR_LEFT: IR.4, U1.34 (GP28)
IR_RIGHT: IR.6, U1.32 (GP27)
LCD_CS: LCD.5, U1.10 (GP7)
unnamed: POWER.K (C), R3.2
unnamed: MTR.A, R2.2
unnamed: C9.-, SPEAKER.- (2)
unnamed: C9.+, R7.2
NEO: R12.1, U1.17 (GP13)
NEO_IN: D1.DI, R12.2
NEO_PWR: C2.2, D1.VCC, IN4148.C
PWR: AUX_5V.3, C1.1, C3.2, IN4148.A, IR.1, JP4.1, LCD.1, LSP2.MP, LSP4.MP, PMEG.C, PMEG3050.C, POWER.A, SERVO.2, U1.39 (VSYS), WHEELA2.4, WHEELB2.4
RST: LCD.7, U1.27 (GP21)
RX0: 3V3ZENER.A, PI.4, R1.2, U1.22 (GP17)
RX5V: AUX_5V.2, R1.1
SCL1: I2C_1.1, R5.1, U1.25 (GP19)
SDA1: I2C_1.2, R4.1, U1.24 (GP18)
SERVO: SERVO.3, U1.26 (GP20)
SPI_SCK: LCD.4, U1.4 (GP2)
SPI_TX: LCD.3, U1.5 (GP3)
SPKR: R7.1, U1.29 (GP22)
STBY: JP4.6, R2.1, SW1.2
TX0: AUX_5V.1, PI.5, U1.21 (GP16)
USB5V: LSP1.MP, PI.1, PI.2, PMEG3050.A, U1.40 (VBUS)
VCC: C5.2, I2C_1.3, IR.3, R4.2, R5.2, RN1.1, SW1.1 (S), U1.36 (3V3(OUT))

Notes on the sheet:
Motor Disable
5V Power
+3.3v
Header for IR sensors
Pushbutton
I2C
1N4148
Speaker
H-Bridge
FLT
SLEEP
GP10/11 A Motors GP04/05 A encoders GP08/09 B motors GP00/01 B encoders GP27 IR left GP28 IR right GP26 IR center GP22 Speaker GP13 Neopixel GP20 Servo GP12 Button GP14/15 Bump L/R GP18/19 dist SDA1/SCL1 GP16/17 i2c SDA/SCL
1N5821
Backlight is always on, use jumper if LCD needs pin pulled high
Changes from rev f (2022) Pin legend text corrected bump connector moved slighly LCD connector moved toward pico Motor switch on/off reversed
Bump
LCD SPI_Tx GP03 SPI_Ck GP02 SPI_Din GP06 LCD_CS GP07 LCD_Rst GP21
Pi Tx
Pi Rx
5 Volt I2C on Bus 0 or Serial
3.3Volt I2C on Bus 1

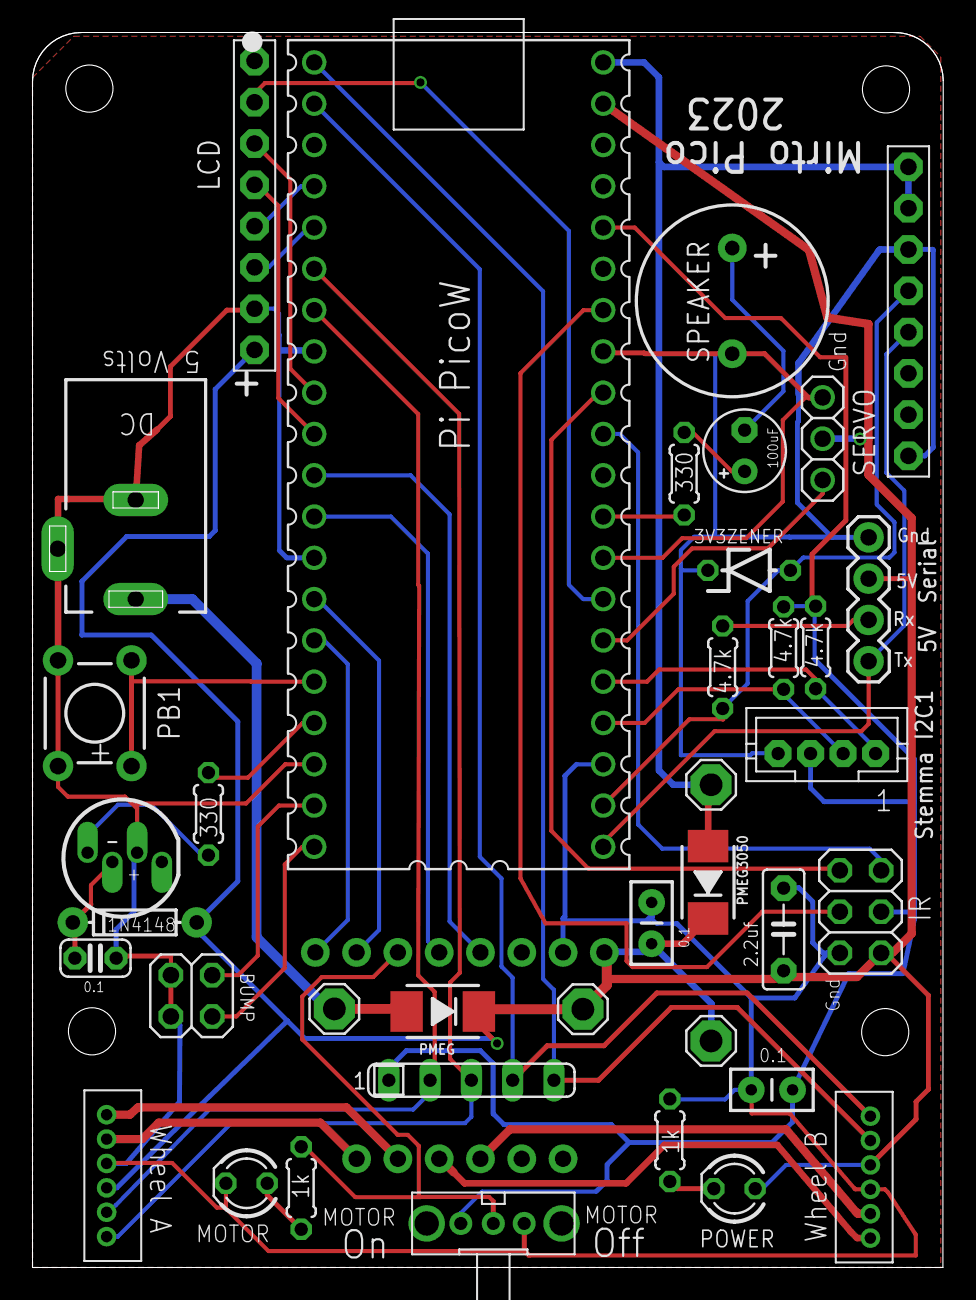
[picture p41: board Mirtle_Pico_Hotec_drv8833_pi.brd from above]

Board: 2 copper layers, 56.0 x 76.0 mm, 42 parts (0 on the bottom side), 43 nets.

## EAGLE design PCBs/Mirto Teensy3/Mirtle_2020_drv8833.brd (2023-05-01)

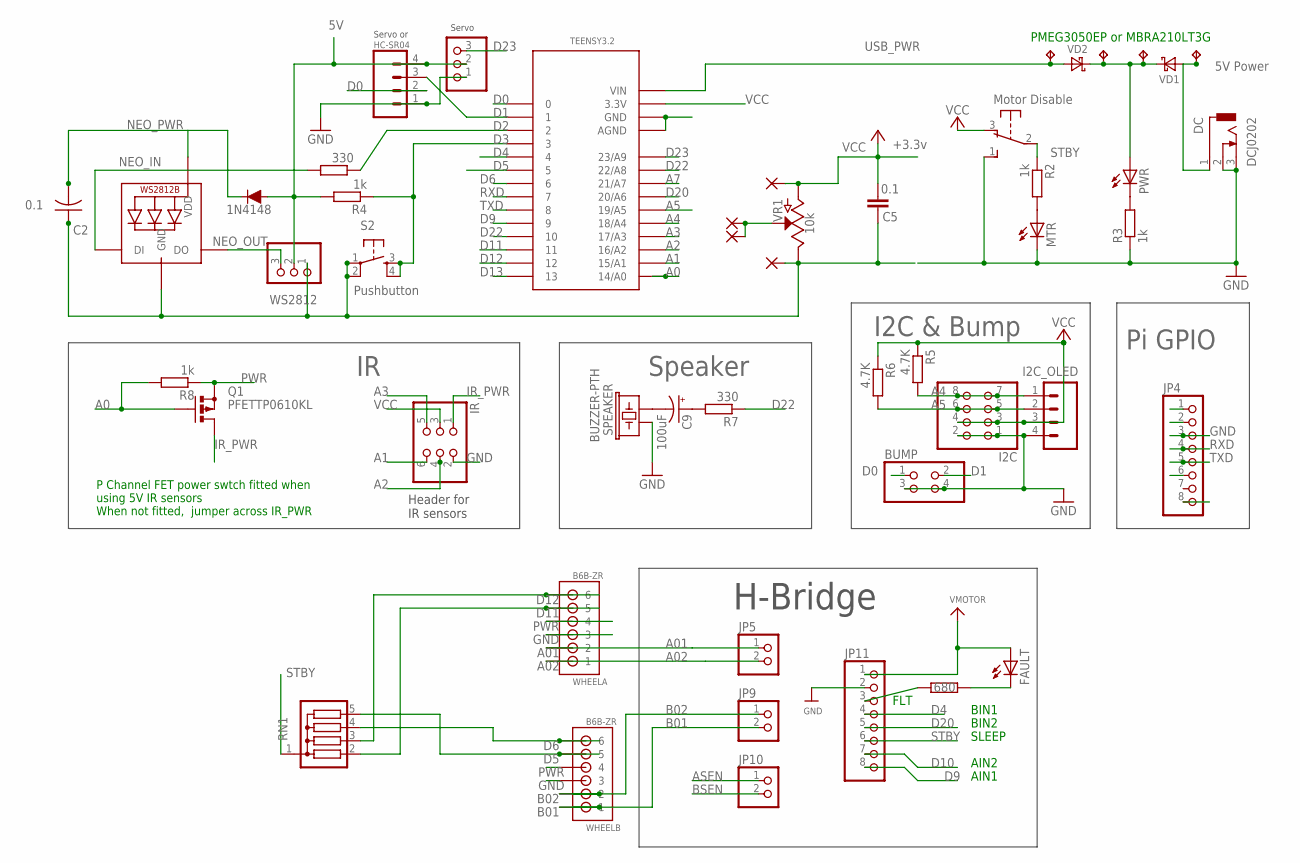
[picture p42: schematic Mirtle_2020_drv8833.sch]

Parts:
BUMP: PINHD-2X2; 2X02
C2: 0.1; C025-024X044
C5: 0.1; CAP-PTH-SMALLEZ
C9: 100uF; E2,5-5
DC: DCJ0202
EXT: PINHD-1X3; 1X03
FAULT: LED3MM
HC-SR04: CONN_04; 1X04
I2C: PINHD-2X4; 2X04
I2C_OLED: CONN_04; 1X04
IN4148: 200mA/100V/1V; DIODE-1N4148
IR: PINHD-2X3; 2X03
JP4: PINHD-1X8BIG; 1X08-BIG
JP5, JP9, JP10: HEADER-1X2ROUND; 1X02_ROUND
JP11: HEADER-1X870MIL; 1X08_ROUND_70
LED1: WS2812B5050; WS2812B
MTR: LED3MM
PAD6, PAD7, PAD8, PAD9: 1,6/0,8
PWR: LED3MM
Q1: PFETTP0610KL; TO92-OVAL
R1: 680; 0204/7
R2, R3, R4, R8: 1k; 0204/5
R5, R6: 4.7K; 0204/7
R7, R12: 330; 0204/7
RN1: G04R; SIL5
S2: TAC_SWITCHPTH; TACTILE-PTH
SPEAKER: BUZZER-PTH; BUZZER-12MM
SW1: OS102011MA1Q
TEENSY3.2: TEENSY_3.0_BASIC
TP1, TP2, TP3, TP4: TPPAD1-13; P1-13
VD1, VD2: DIODE-SCHOTTKY-SMA; SMA
VR1: 10k; POT-PTH-ALPS-KIT
WHEELA: B6B-ZR
WHEELB: B6B-ZR
WS2812: PINHD-1X3; 1X03

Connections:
5VIN: DC.1, TP1.TP, VD1.A
A0: Q1.2 (G), R8.2, TEENSY3.2.14/A0
A1: IR.6, TEENSY3.2.15/A1
A01: JP5.1, WHEELA.2
A2: IR.4, TEENSY3.2.16/A2
A02: JP5.2, WHEELA.1
A3: IR.5, TEENSY3.2.17/A3
A4: I2C.7, I2C.8, I2C_OLED.1, R5.2, TEENSY3.2.18/A4
A5: I2C.5, I2C.6, I2C_OLED.2, R6.2, TEENSY3.2.19/A5
A7: PAD6.1, PAD9.1, TEENSY3.2.21/A7, VR1.P$2 (S)
ASEN: JP10.1
B01: JP9.2, WHEELB.1
B02: JP9.1, WHEELB.2
BSEN: JP10.2
D0: BUMP.1, HC-SR04.2, TEENSY3.2.0
D1: BUMP.2, HC-SR04.3, TEENSY3.2.1
D2: R12.1, TEENSY3.2.2
D3: R4.1, S2.3, S2.4, TEENSY3.2.3
D4: JP11.4, TEENSY3.2.4
D5: RN1.5, TEENSY3.2.5, WHEELB.5
D6: RN1.4, TEENSY3.2.6, WHEELB.6
D9: JP11.8, TEENSY3.2.9
D10: JP11.7, TEENSY3.2.10
D11: RN1.2, TEENSY3.2.11, WHEELA.5
D12: RN1.3, TEENSY3.2.12, WHEELA.6
D13: TEENSY3.2.13
D20: JP11.5, TEENSY3.2.20/A6
D22: R7.1, TEENSY3.2.22/A8
D23: EXT.3, TEENSY3.2.23/A9
GND: BUMP.3, BUMP.4, C2.1, C5.1, DC.2, DC.3, EXT.1, HC-SR04.1, I2C.1, I2C.2, I2C_OLED.4, IR.2, JP4.3, JP4.8, JP11.2, LED1.3-GND (GND), MTR.K (C), PAD8.1, R3.1, S2.1, S2.2, SPEAKER.+ (1), SW1.1 (S), TEENSY3.2.AGND, TEENSY3.2.GND, VR1.P$1 (E), WHEELA.3, WHEELB.3, WS2812.1
IR_PWR: IR.1, Q1.3 (D)
unnamed: JP11.3, R1.1
unnamed: FAULT.K (C), R1.2
unnamed: PWR.K (C), R3.2
unnamed: MTR.A, R2.2
unnamed: C9.-, SPEAKER.- (2)
unnamed: C9.+, R7.2
NEO_IN: LED1.4-DIN (DI), R12.2
NEO_OUT: LED1.2-DOUT (DO), WS2812.3
NEO_PWR: C2.2, IN4148.C, LED1.1-VDD (VDD)
PWR: EXT.2, FAULT.A, HC-SR04.4, IN4148.A, JP4.1, JP4.2, JP11.1, PWR.A, Q1.1 (S), R4.2, R8.1, TP2.TP, TP3.TP, VD1.C, VD2.C, WHEELA.4, WHEELB.4, WS2812.2
RXD: JP4.4, TEENSY3.2.7
STBY: JP11.6, R2.1, RN1.1, SW1.2
TXD: JP4.5, TEENSY3.2.8
USB_PWR: TEENSY3.2.VIN, TP4.TP, VD2.A
VCC: C5.2, I2C.3, I2C.4, I2C_OLED.3, IR.3, PAD7.1, R5.1, R6.1, SW1.3 (O), TEENSY3.2.3.3V, VR1.P$3 (A)

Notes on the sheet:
Motor Disable
5V Power
+3.3v
Servo or
Header for IR sensors
Pushbutton
H-Bridge
Pi GPIO
I2C & Bump
PMEG3050EP or MBRA210LT3G
P Channel FET power swtch fitted when using 5V IR sensors When not fitted, jumper across IR_PWR
1N4148
FLT
BIN1
BIN2
SLEEP
AIN2
AIN1
Servo
Speaker

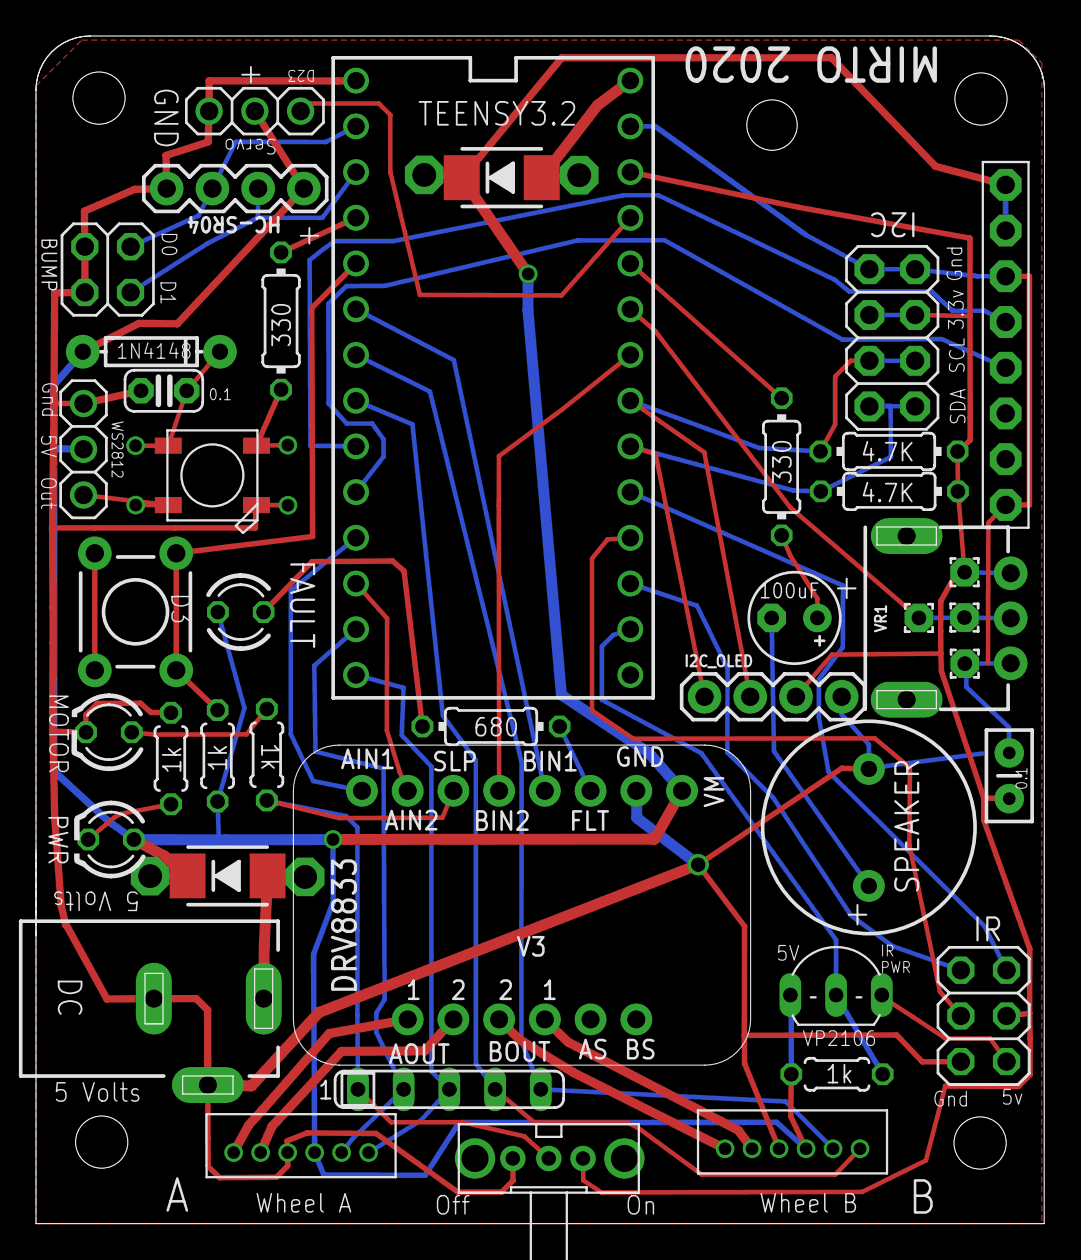
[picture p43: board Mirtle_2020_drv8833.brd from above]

Board: 4 copper layers, 56.0 x 66.0 mm, 49 parts (0 on the bottom side), 43 nets.

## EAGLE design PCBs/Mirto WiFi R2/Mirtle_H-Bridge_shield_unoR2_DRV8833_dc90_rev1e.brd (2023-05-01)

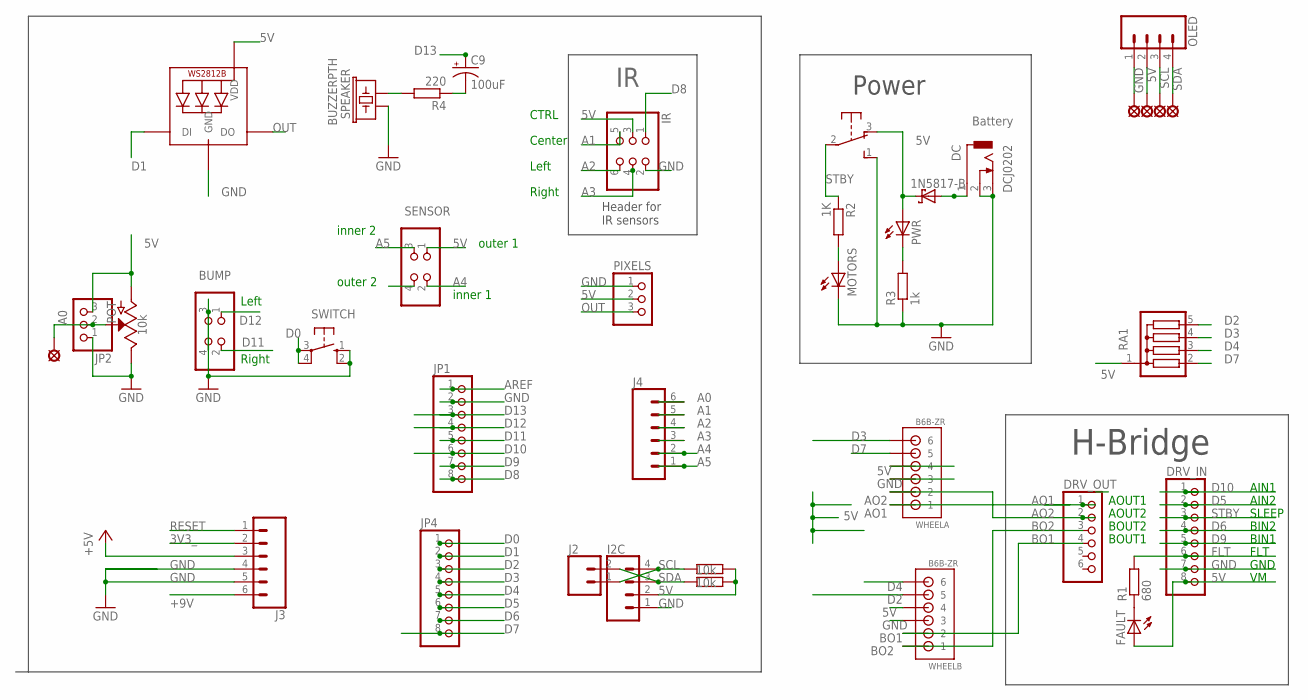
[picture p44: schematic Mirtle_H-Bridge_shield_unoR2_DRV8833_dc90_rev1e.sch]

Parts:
BUMP: PINHD-2X2; 2X02
C9: 100uF; E2,5-5
D1: 1N5817-B; DO41-7.6
DC: DCJ0202
DRV_IN: HEADER-1X870MIL; 1X08_ROUND_70
DRV_OUT: PINHD-1X6CLEAN; 1X06-CLEAN
FAULT: LED3MM
I2C: CONN_04; 1X04
IR: PINHD-2X3; 2X03
J2: CONN_02; 1X02
J3, J4: CONN_06NO_SILK_FEMALE_PTH; 1X06_NO_SILK
JP1, JP4: PINHD-1X8CLEANBIG; 1X08-CLEANBIG
JP2: PINHD-1X3CB; 1X03-CLEANBIG
LED1: WS2812B5050; WS2812B
LSP1, LSP13, LSP14, LSP15, LSP16: LSP10
MOTORS: LED3MM
OLED: CONN_04; 1X04
PIXELS: PINHD-1X3; 1X03
POT: 10k; POT-PTH-ALPS
PWR: LED3MM
R1: 680; 0204/5
R2: 1K; 0204/5
R3: 1k; 0204/5
R4: 220; 0204/5
R5, R6: 10k; 0204/5
RA1: G04R; SIL5
SENSOR: PINHD-2X2; 2X02
SPEAKER: BUZZERPTH; BUZZER-12MM
SW1: OS102011MA1Q
SWITCH: 10-XX; B3F-10XX
WHEELA: B6B-ZR
WHEELB: B6B-ZR

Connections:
3V3_: J3.2
5V: D1.C, DRV_IN.8, FAULT.A, I2C.2, IR.3, J3.3, JP2.3, LED1.1-VDD (VDD), LSP14.MP, OLED.2, PIXELS.2, POT.P$3 (A), PWR.A, R5.1, R6.1, RA1.1, SENSOR.1, SW1.3 (O), WHEELA.4, WHEELB.4
5VIN: D1.A, DC.1
+9V: J3.6
A0: J4.6, JP2.2, LSP1.MP, POT.P$2 (S)
A1: IR.5, J4.5
A2: IR.6, J4.4
A3: IR.4, J4.3
A4: J4.2, SENSOR.2
A5: J4.1, SENSOR.3
AO1: DRV_OUT.1, WHEELA.1
AO2: DRV_OUT.2, WHEELA.2
AREF: JP1.1
BO1: DRV_OUT.4, WHEELB.2
BO2: DRV_OUT.3, WHEELB.1
D0: JP4.1, SWITCH.3, SWITCH.4 (P1)
D1: JP4.2, LED1.4-DIN (DI)
D2: JP4.3, RA1.5, WHEELB.5
D3: JP4.4, RA1.4, WHEELA.6
D4: JP4.5, RA1.3, WHEELB.6
D5: DRV_IN.2, JP4.6
D6: DRV_IN.4, JP4.7
D7: JP4.8, RA1.2, WHEELA.5
D8: IR.1, JP1.8
D9: DRV_IN.5, JP1.7
D10: DRV_IN.1, JP1.6
D11: BUMP.2, JP1.5
D12: BUMP.1, JP1.4
D13: C9.+, JP1.3
FLT: DRV_IN.6, R1.2
GND: BUMP.3, BUMP.4, DC.2, DC.3, DRV_IN.7, I2C.1, IR.2, J3.4, J3.5, JP1.2, JP2.1, LED1.3-GND (GND), LSP13.MP, MOTORS.K (C), OLED.1, PIXELS.1, POT.P$1 (E), R3.1, SENSOR.4, SPEAKER.+ (1), SW1.1 (S), SWITCH.1 (S), SWITCH.2 (S1), WHEELA.3, WHEELB.3
unnamed: PWR.K (C), R3.2
unnamed: R4.2, SPEAKER.- (2)
unnamed: C9.-, R4.1
unnamed: FAULT.K (C), R1.1
unnamed: MOTORS.A, R2.2
OUT: LED1.2-DOUT (DO), PIXELS.3
RESET: J3.1
SCL: I2C.4, J2.1, LSP15.MP, OLED.3, R5.2
SDA: I2C.3, J2.2, LSP16.MP, OLED.4, R6.2
STBY: DRV_IN.3, R2.1, SW1.2

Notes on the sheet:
Battery
Header for IR sensors
H-Bridge
GND
AIN1
AIN2
SLEEP
BIN1
BIN2
FLT
Center
CTRL
Left
Right
AOUT1
AOUT2
BOUT2
BOUT1
Power
outer 1
outer 2
inner 1
inner 2

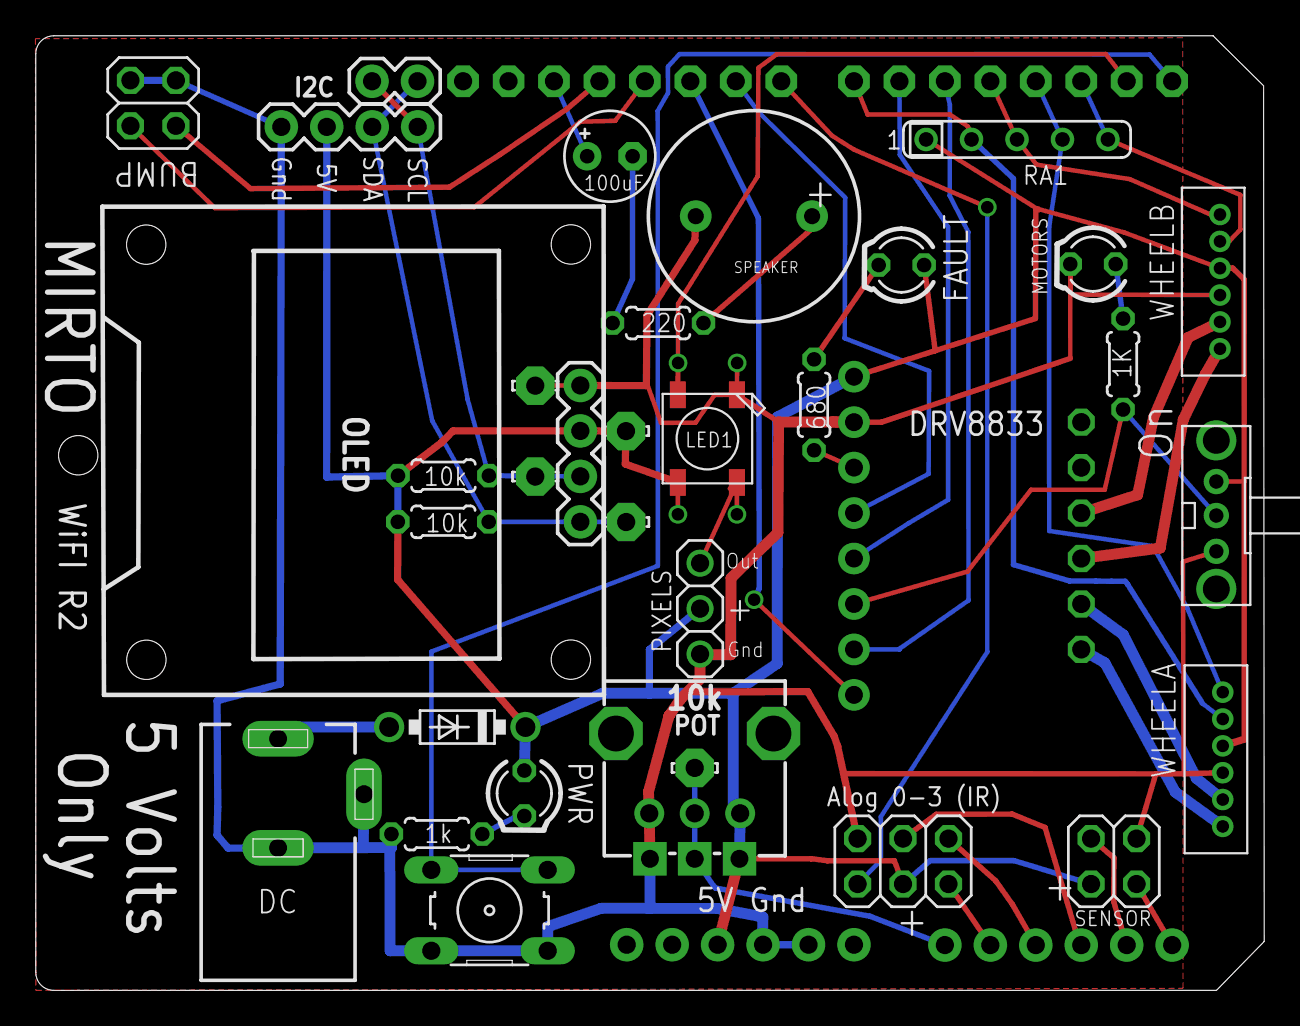
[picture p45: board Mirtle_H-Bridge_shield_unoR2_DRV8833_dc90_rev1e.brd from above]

Board: 2 copper layers, 68.6 x 53.3 mm, 39 parts (0 on the bottom side), 37 nets.

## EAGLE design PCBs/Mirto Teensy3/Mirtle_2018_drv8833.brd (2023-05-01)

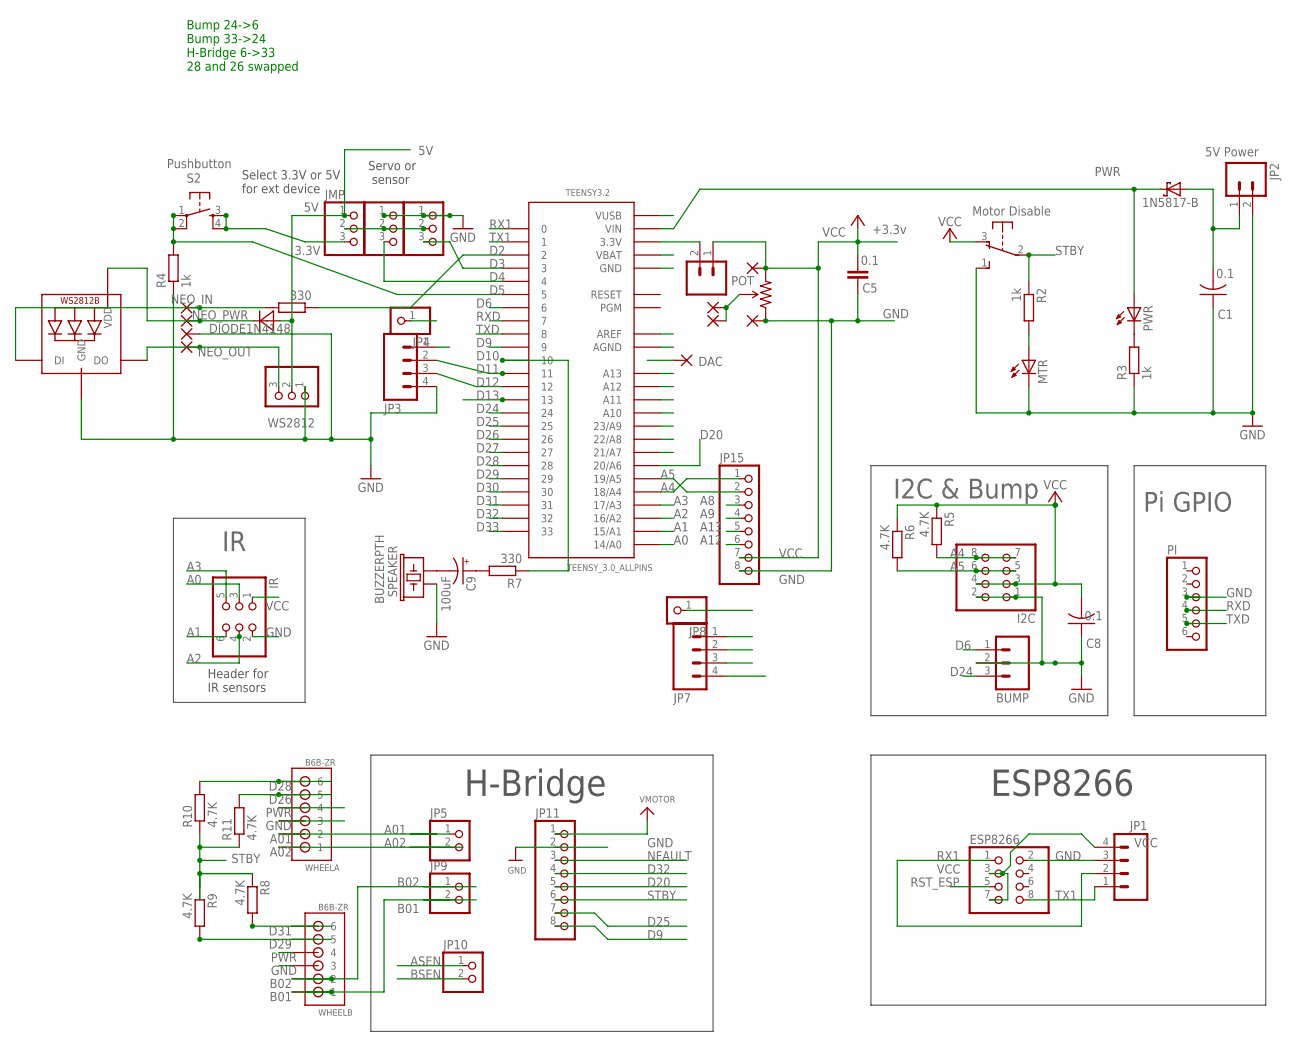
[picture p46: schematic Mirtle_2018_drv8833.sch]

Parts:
3V3: M02PTH; 1X02
BUMP: M03SCREW; SCREWTERMINAL-3.5MM-3
C1, C8: 0.1; C025-024X044
C5: 0.1; CAP-PTH-SMALLEZ
C9: 100uF; E2,5-5
D1: 1N5817-B; DO41-7.6
D3: DIODE1N4148; DO-35
DAC: 1,6/0,8
ESP8266: PINHD-2X4; 2X04
EXT, EXT1: PINHD-1X3; 1X03
I2C: PINHD-2X4; 2X04
IR: PINHD-2X3; 2X03
JMP: PINHD-1X3; 1X03
JP1, JP3, JP7: M04PTH; 1X04
JP2: M023.5MM; SCREWTERMINAL-3.5MM-2
JP4, JP8: PINHD-1X1; 1X01
JP5, JP9, JP10: HEADER-1X2ROUND; 1X02_ROUND
JP11: HEADER-1X870MIL; 1X08_ROUND_70
JP15: PINHD-1X8BIG; 1X08-BIG
LED1: WS2812B5050; WS2812B
MTR: LED3MM
PAD2, PAD3, PAD4, PAD5, PAD6, PAD7, PAD8, PAD9: 1,6/0,8
PI: PINHD-1X6; 1X06
POT: TSR-3386; 3386U
PWR: LED3MM
R2, R3, R4: 1k; 0204/7
R5, R6: 4.7K; 0204/7
R7: 330; 0204/7
R8, R9, R10, R11: 4.7K; 0204/5
R12: 330; 0204/5
S2: TAC_SWITCHPTH; TACTILE-PTH
SPEAKER: BUZZERPTH; BUZZER-12MM
SW1: OS102011MA1Q
TEENSY3.2: TEENSY_3.0_ALLPINS
WHEELA: B6B-ZR
WHEELB: B6B-ZR
WS2812: PINHD-1X3; 1X03

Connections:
5VIN: C1.2, D1.A, JP2.1
A0: IR.3, TEENSY3.2.14/A0
A1: IR.6, TEENSY3.2.15/A1
A01: JP5.1, WHEELA.2
A2: IR.4, TEENSY3.2.16/A2
A02: JP5.2, WHEELA.1
A3: IR.5, TEENSY3.2.17/A3
A4: I2C.7, I2C.8, JP7.1, JP15.1, R5.2, TEENSY3.2.18/A4
A5: I2C.5, I2C.6, JP8.1, JP15.2, R6.2, TEENSY3.2.19/A5
A7: PAD6.1, PAD9.1, POT.2 (WIPER), TEENSY3.2.21/A7
A8: JP15.3, TEENSY3.2.22/A8
A9: JP15.4, TEENSY3.2.23/A9
A10: TEENSY3.2.A10
A11: TEENSY3.2.A11
A12: JP15.6, TEENSY3.2.A12
A13: JP15.5, TEENSY3.2.A13
ASEN: JP10.1
B01: JP9.2, WHEELB.1
B02: JP9.1, WHEELB.2
BSEN: JP10.2
D2: R12.1, TEENSY3.2.2
D3: EXT.3, TEENSY3.2.3
D4: EXT1.3, TEENSY3.2.4
D5: R4.2, S2.1, S2.2, TEENSY3.2.5
D6: BUMP.1, TEENSY3.2.6
D9: JP11.8, TEENSY3.2.9
D10: R7.1, TEENSY3.2.10
D11: JP3.2, TEENSY3.2.11
D12: JP3.3, TEENSY3.2.12
D13: JP7.4, TEENSY3.2.13
D20: JP11.5, TEENSY3.2.20/A6
D24: BUMP.3, TEENSY3.2.24
D25: JP11.7, TEENSY3.2.25
D26: R11.2, TEENSY3.2.26, WHEELA.5
D27: TEENSY3.2.27
D28: R10.2, TEENSY3.2.28, WHEELA.6
D29: R9.2, TEENSY3.2.29, WHEELB.5
D30: TEENSY3.2.30
D31: R8.2, TEENSY3.2.31, WHEELB.6
D32: JP11.4, TEENSY3.2.32
D33: TEENSY3.2.33
GND: BUMP.2, C1.1, C5.1, C8.1, ESP8266.2, EXT.1, EXT1.1, I2C.1, I2C.2, IR.2, JP1.3, JP2.2, JP3.4, JP7.3, JP11.2, JP15.8, LED1.3-GND (GND), MTR.K (C), PAD4.1, PAD8.1, PI.3, POT.1 (CCW), R3.1, R4.1, SPEAKER.+ (1), SW1.1 (S), TEENSY3.2.AGND, TEENSY3.2.GND, TEENSY3.2.GND1 (GND), TEENSY3.2.GND2 (GND), WHEELA.3, WHEELB.3, WS2812.1
unnamed: PWR.K (C), R3.2
unnamed: 3V3.2, TEENSY3.2.3.3V, TEENSY3.2.3.3V1 (3.3V), TEENSY3.2.3.3V2 (3.3V)
unnamed: MTR.A, R2.2
unnamed: EXT.2, EXT1.2, JMP.2
unnamed: C9.-, SPEAKER.- (2)
unnamed: C9.+, R7.2
NEO_IN: LED1.4-DIN (DI), PAD2.1, R12.2
NEO_OUT: LED1.2-DOUT (DO), PAD5.1, WS2812.3
NEO_PWR: D3.-, LED1.1-VDD (VDD), PAD3.1
NFAULT: JP11.3
PWR: D1.C, D3.+, JMP.1, JP11.1, PWR.A, TEENSY3.2.VIN, WHEELA.4, WHEELB.4, WS2812.2
RST_ESP: ESP8266.5
RX1: ESP8266.1, JP1.2, JP3.1, TEENSY3.2.0
RXD: PI.4, TEENSY3.2.7
STBY: JP11.6, R2.1, R8.1, R9.1, R10.1, R11.1, SW1.2
TX1: ESP8266.8, JP1.1, JP4.1, TEENSY3.2.1
TXD: PI.5, TEENSY3.2.8
VCC: 3V3.1, C5.2, C8.2, ESP8266.3, ESP8266.7, I2C.3, I2C.4, IR.1, JMP.3, JP1.4, JP7.2, JP15.7, PAD7.1, POT.3 (CW), R5.1, R6.1, S2.3, S2.4, SW1.3 (O)

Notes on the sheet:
Motor Disable
5V Power
+3.3v
3.3V
Servo or sensor
Select 3.3V or 5V for ext device
Header for IR sensors
Pushbutton
H-Bridge
ESP8266
Pi GPIO
I2C & Bump
Bump 24->6 Bump 33->24 H-Bridge 6->33 28 and 26 swapped

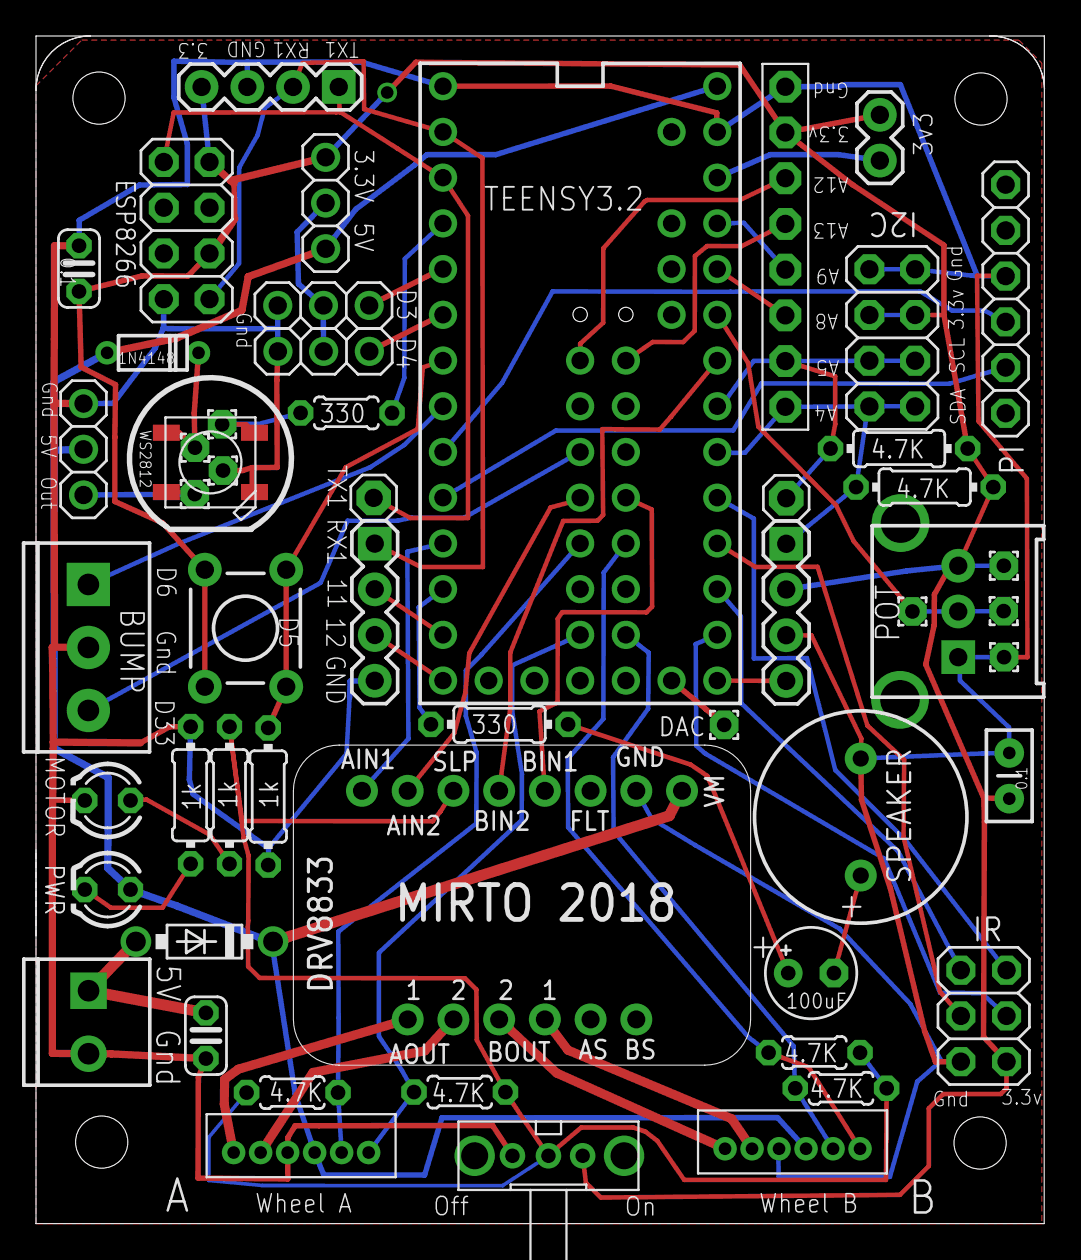
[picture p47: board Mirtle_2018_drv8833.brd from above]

Board: 2 copper layers, 56.0 x 66.0 mm, 57 parts (0 on the bottom side), 51 nets.

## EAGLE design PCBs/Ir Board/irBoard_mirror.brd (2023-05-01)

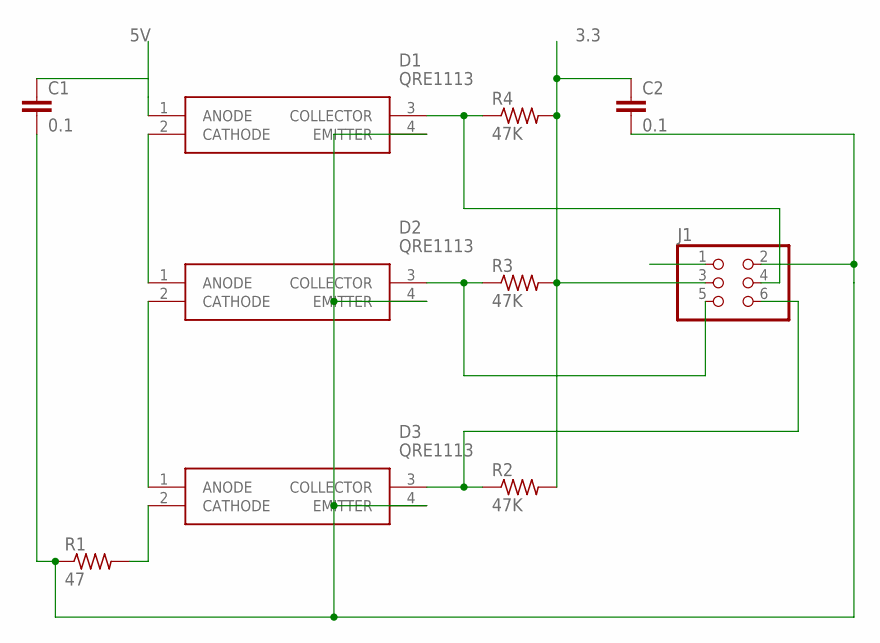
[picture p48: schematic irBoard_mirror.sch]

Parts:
C1, C2: 0.1; C025-024X044
D1, D2, D3: QRE1113
J1: PINHD-2X3; 2X03
R1: 47; 0204/5
R2, R3, R4: 47K; 0204/5

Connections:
3.3: C2.1, J1.3, R2.2, R3.2, R4.2
5V: C1.1, D1.1 (ANODE), J1.1
GND: C1.2, C2.2, D1.4 (EMITTER), D2.4 (EMITTER), D3.4 (EMITTER), J1.2, R1.1
unnamed: D2.2 (CATHODE), D3.1 (ANODE)
unnamed: D1.2 (CATHODE), D2.1 (ANODE)
unnamed: D3.2 (CATHODE), R1.2
unnamed: D1.3 (COLLECTOR), J1.4, R4.1
unnamed: D2.3 (COLLECTOR), J1.5, R3.1
unnamed: D3.3 (COLLECTOR), J1.6, R2.1

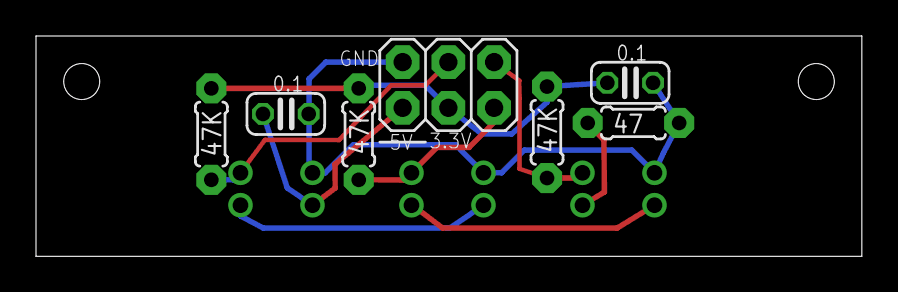
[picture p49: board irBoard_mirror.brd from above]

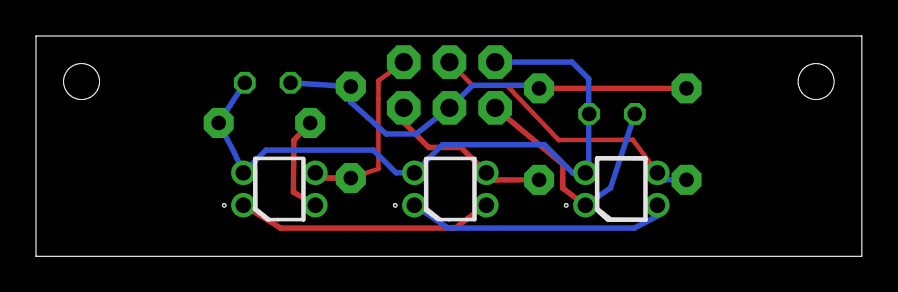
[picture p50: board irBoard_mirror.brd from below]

Board: 4 copper layers, 45.9 x 12.2 mm, 10 parts (3 on the bottom side), 9 nets.

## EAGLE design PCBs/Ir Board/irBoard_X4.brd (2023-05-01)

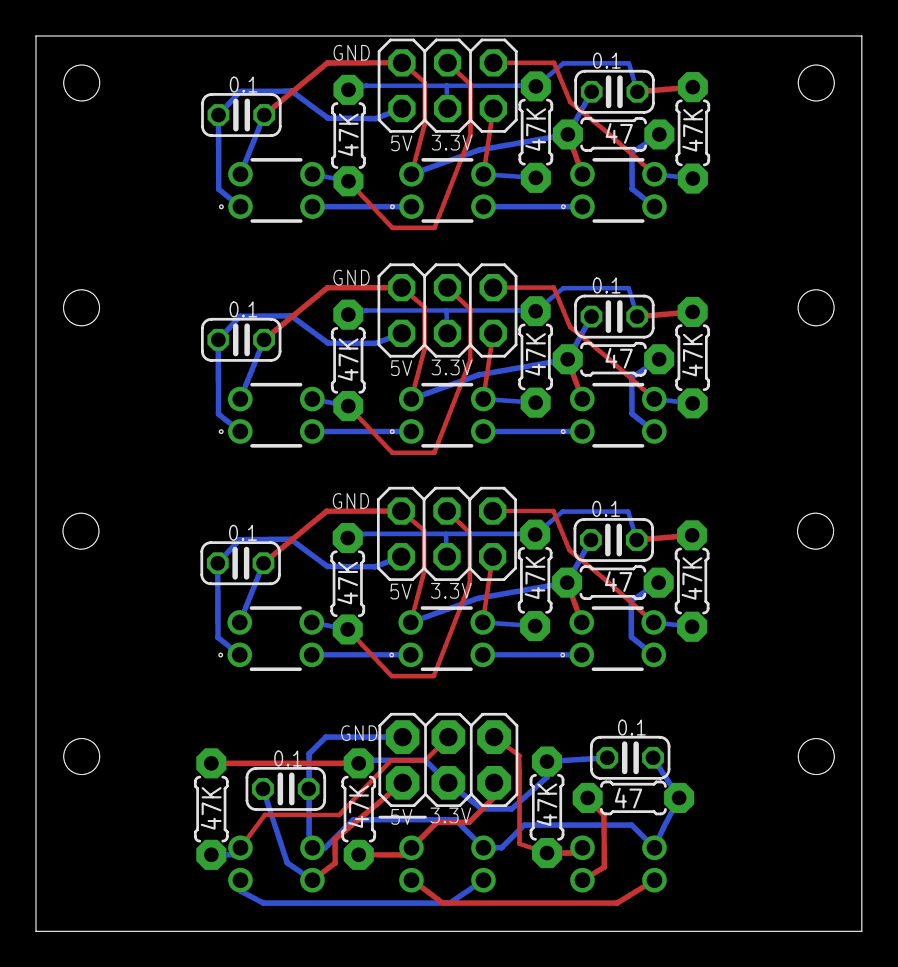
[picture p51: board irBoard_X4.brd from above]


Board: 4 copper layers, 45.9 x 49.7 mm, 40 parts (3 on the bottom side), 36 nets.

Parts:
C1, C2, C3, C4, C5, C6, C9, C10: 0.1; C025-024X044
D1, D2, D3, D4, D5, D6, D7, D8, D9, D13, D14, D15: QRE1113
J1: 2X03
JP1, JP2, JP3: 2X03
R1, R5, R9, R17: 47; 0204/5
R2, R3, R4, R6, R7, R8, R10, R11, R12, R18, R19, R20: 47K; 0204/5

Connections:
3.1: C4.1, JP2.3, R6.2, R7.2, R8.2
3.2: C6.1, JP3.3, R10.2, R11.2, R12.2
3.3: C2.1, J1.3, R2.2, R3.2, R4.2
3.5: C10.1, JP1.3, R18.2, R19.2, R20.2
5V: C1.1, D1.1, J1.1
5V1: C3.1, D4.1, JP2.1
5V2: C5.1, D7.1, JP3.1
5V4: C9.1, D13.1, JP1.1
GND: C1.2, C2.2, D1.4, D2.4, D3.4, J1.2, R1.1
GND1: C3.2, C4.2, D4.4, D5.4, D6.4, JP2.2, R5.1
GND2: C5.2, C6.2, D7.4, D8.4, D9.4, JP3.2, R9.1
GND4: C9.2, C10.2, D13.4, D14.4, D15.4, JP1.2, R17.1
unnamed: D2.2, D3.1
unnamed: D1.2, D2.1
unnamed: D5.2, D6.1
unnamed: D3.2, R1.2
unnamed: D4.2, D5.1
unnamed: D6.2, R5.2
unnamed: D1.3, J1.4, R4.1
unnamed: D2.3, J1.5, R3.1
unnamed: D3.3, J1.6, R2.1
unnamed: D4.3, JP2.4, R8.1
unnamed: D5.3, JP2.5, R7.1
unnamed: D6.3, JP2.6, R6.1
unnamed: D8.2, D9.1
unnamed: D7.2, D8.1
unnamed: D9.2, R9.2
unnamed: D7.3, JP3.4, R12.1
unnamed: D8.3, JP3.5, R11.1
unnamed: D9.3, JP3.6, R10.1
unnamed: D14.2, D15.1
unnamed: D13.2, D14.1
unnamed: D15.2, R17.2
unnamed: D13.3, JP1.4, R20.1
unnamed: D14.3, JP1.5, R19.1
unnamed: D15.3, JP1.6, R18.1

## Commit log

2023-05-01 Initial commit of Mirto 2023 files
    [9g servo mount.SLDPRT, Hotec Motor Mountv2.SLDPRT, Mirtle_2018_drv8833.brd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]
2023-05-01 added mirto 2020 pcb
    [Mirtle_2020_drv8833.brd, Mirtle_2020_drv8833.sch]
2023-05-02 added spreadsheet BOM with supplier part numbers
    [Hotec Motor Mountv2.SLDPRT, Mirto BOM.xlsx, Motor hub.SLDPRT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]
2023-05-02 updated link to BOM
    [Mirto_BOM.xlsx]
2023-05-02 updated dxf to improve import into lotus cut
    [arduino robot half sheet r12.dxf, one mirto2023.dxf]
2023-06-03 updated build doc updated bumper dxf
    [Mirtle_Pico_Hotec_drv8833_pi.brd, Mirtle_Pico_Hotec_drv8833_pi.sch, Motor hub.SLDPRT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]
2023-08-14 updated solidworks parts
    [9g servo mount.SLDPRT, Hotec Motor Mountv2.SLDPRT, Motor hub.SLDPRT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]
2024-08-22 update BOM - added 2.2uf Cap and BAT46 diode
    [Mirto_BOM.xlsx]

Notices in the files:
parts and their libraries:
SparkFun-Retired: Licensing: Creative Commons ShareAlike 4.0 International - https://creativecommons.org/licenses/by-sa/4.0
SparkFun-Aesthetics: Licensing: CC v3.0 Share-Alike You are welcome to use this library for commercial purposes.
